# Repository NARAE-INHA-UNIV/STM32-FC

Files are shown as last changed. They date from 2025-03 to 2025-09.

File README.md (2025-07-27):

**본 문서는 STM32 firmware만을 다루고 있습니다.**

> [[STM32-FC-docs]](https://github.com/NARAE-INHA-UNIV/STM32-FC-docs) How to use, Specification <br>
> [[STM32-FC-hw]](https://github.com/NARAE-INHA-UNIV/STM32-FC-hw) KiCAD, Schematic, PCB Artwork <br>
> [[MiniLink_cli]](https://github.com/NARAE-INHA-UNIV/MiniLink_cli) Data analysis like msg, log, param <br>

-----

# STM32 FC

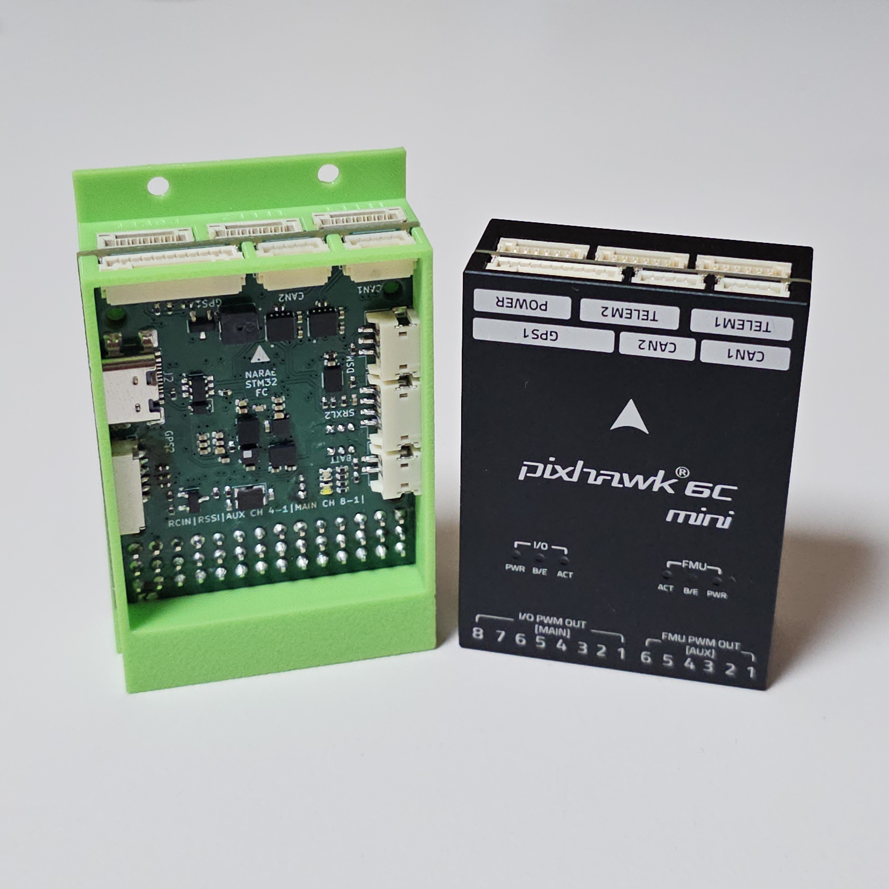
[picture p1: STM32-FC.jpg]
pcb img


인하대학교 모형항공기 동아리 나래에서 2024년 동계 UAV 활동으로 진행한 프로젝트임. <br>
회로와 펌웨어를 개발하되, 기성 pixhawk 모듈과 호환성을 가지기 위해 pixhawk 6C mini의 인터페이스와 흡사하게 제작하는 것을 목표로함. <br>

- 활동명 : [UAV] FC 제작 활동
- 일시 : 2024 동계 방학 - 진행중
- 팀명 :  항공전자 (구 FC)
- 팀장 : 정영우(2025), 이현제(2024)

## 폴더 구조

`Plane` 폴더가 STM32Cube IDE 프로젝트이다. 주로 수정할 코드는 `Core` 디렉토리 내에 위치한다.

`Plane` -> `Core` -> `Src/Inc`

- Src : Source code (.c)
- Inc : header (.h)
  - {Module Name}.h
  - {Module Name}_module.h
  - {Module Name}_common.h
  - {Module Name}_type.h

{Module Name} 앞의 접두사의 의미 :
- `FC` : 보드 내부 HW 관리 (UART, RC, Servo etc.)
- `AP` : 고수준의 제어기나 자율 비행 (Failsafe, RTH etc.)
- `SEN` : 외부 센서

헤더 파일 중 `driver.h`는 외부 모듈에서 접근할 떄 사용한다. <br>
예를 들어 `main.c`가 `RadioContol` 모듈에 접근할 때 `FC_RC/driver.h`에 접근해야 한다. `RadioContol.h`는 해당 모듈 내부에서 사용하는 코드로 외부에서 직접 접근하지 않도록 한다.

```bash
├─AP_Failsafe       # Failsafe 관련 코드
├─FC_AHRS           # IMU 센서, 기압 센서
├─FC_Basic          # Buzzer나 LED 등
├─FC_RC             # 라디오 조종기 (스펙트럼, PPM, ELRS)
├─FC_Servo          # 서보 모터, ESC
├─FC_Serial         # Serial 기능
│  └─MiniLink       # 외부 장치와 통신하는 프로토콜
│      └─Param      # 파라미터 관리
└─test              # 테스트 중인 코드
```

## 기여 (개발)

1. 프로젝트 fork
2. fork된 개인 레파지토리 clone
3. 코드 작성
4. 개인 레파지토리에 커밋 & 푸시
5. Pull-request

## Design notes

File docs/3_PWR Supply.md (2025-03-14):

# 3. 전원 공급시 주의사항

| **보드는 하나의 전원으로부터 5V를 공급 받아야 한다.**

보드는 `5V` 라인과  `5V_PWR` 라인으로 나뉜다.
- `5V` 라인은 칩셋과 센서 등 내부 장치와 GPS, 텔레메트리 등 외부장치를 구동한다.
- `5V_PWR`은 ESC와 서보모터 등 `SERVO OUT` 핀에 연결되어 있다.
- 일반적으로 `5V`와 `5V_PWR`은 분리되어 있으나, 필요에 따라 스위치를 통해 연결할 수 있다. 이 경우 둘 이상의 전원이 발생하지 않도록 유의한다.

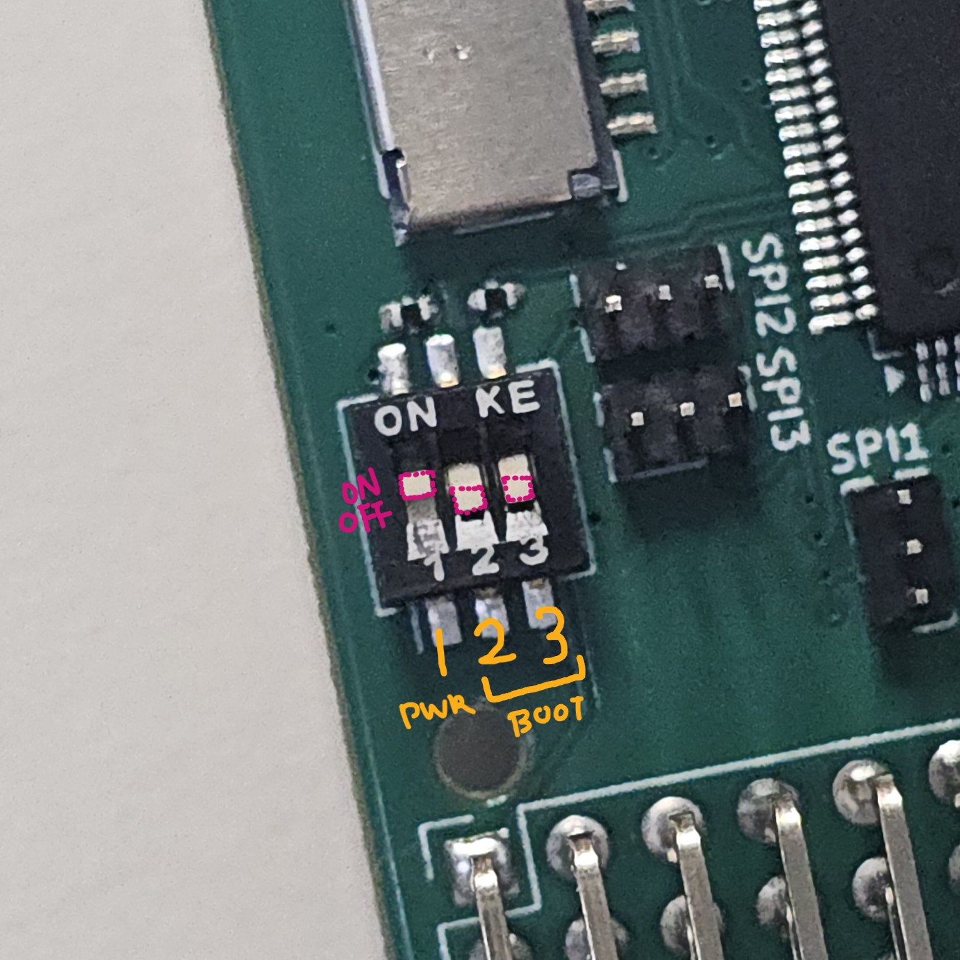
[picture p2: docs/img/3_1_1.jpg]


스위치 1번이 두 전원 라인을 연결하는 데 사용한다. 일반적으로 `OFF` 상태가 기본값이다. 

- ON : 연결
- OFF (Default) : 차단

보드에서 `SERVO OUT` 측 기기로 전원을 공급하거나, `SERVO OUT`에 연결된 ESC로부터 전원을 공급 받을 때 `ON`으로 변경한다.

아래는 전원을 공급하는 세가지 방법에 대해 설명한다.

## 1. USB를 통한 공급 (개발용)

USB를 통해 전원을 공급할 수 있다. 이 경우에 다음 사항에 유의해야 한다.
- USB A to C 케이블만 사용 가능
- 고부하 사용 금지

USB 선을 통해 공급할 수 있는 전력의 한계가 있으므로, 별도의 전원 없이 다수의 서보 모터를 구동하면 보드가 손상될 수 있다.

별도의 배터리가 필요 없어 개발 과정에서 유용하지만, 비행할 수 없으므로 후술할 방법도 익혀야한다.

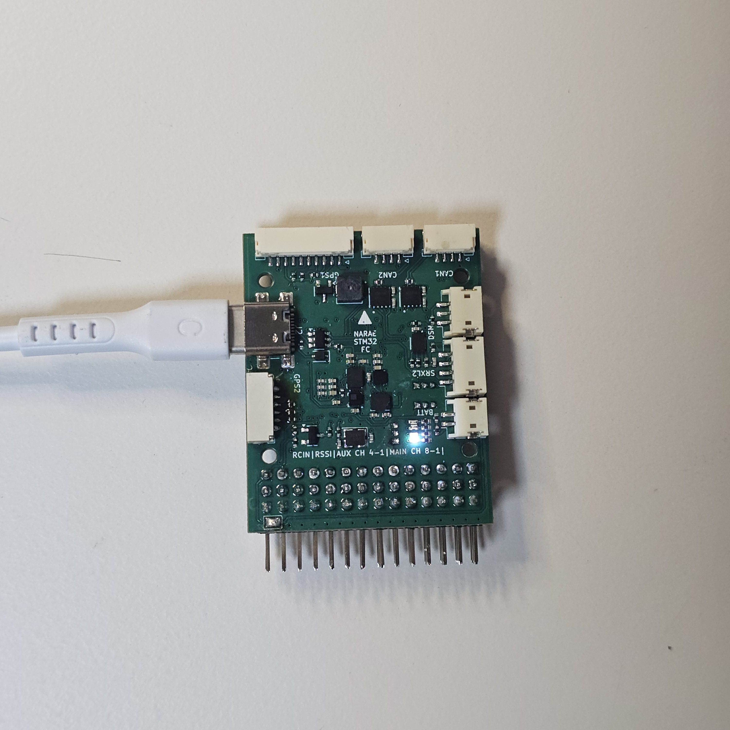
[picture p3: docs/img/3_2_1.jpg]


## 2. 픽스호크의 파워모듈을 통한 공급 (권장)

픽스호크(Pixhawk)사의 파워모듈을 통해 전원을 공급하는 것으로 가장 안전하므로 권장하는 방법이다. 

픽스호크에는 다양한 파워모듈이 존재하며, 이중 **아날로그 모듈**을 사용해야 한다. 예를 들어 `PM02`와 `PM02D`에서 PM02D는 디지털 버전이므로 사용할 수 없다. 두 모델은 연결 커넥터가 다르므로 혼용할 가능성은 없다.

권장하는 모델은 다음과 같다.
- 1개의 ESC와 모터를 사용하는 단발 고정익기인 경우 : PM02
- 2개 이상의 ESC를 사용하는 고정익기 또는 멀티콥터 : PM06

파워 모듈은 보드의 `POWER` 커넥터에 연결한다.

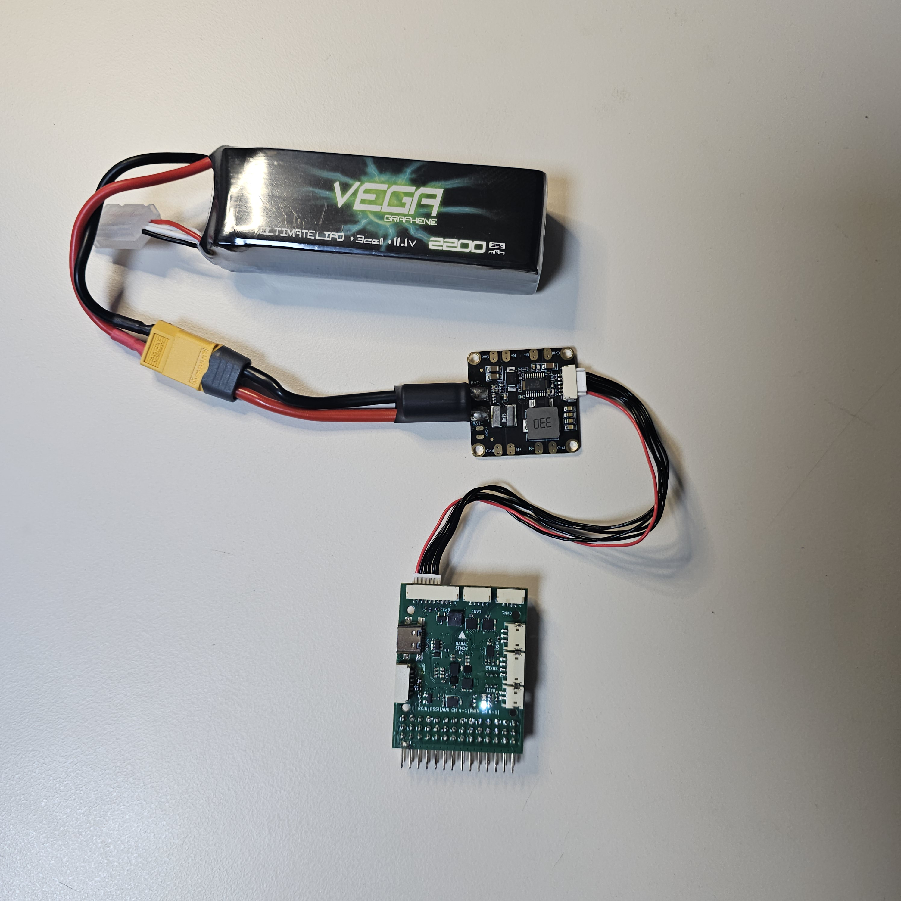
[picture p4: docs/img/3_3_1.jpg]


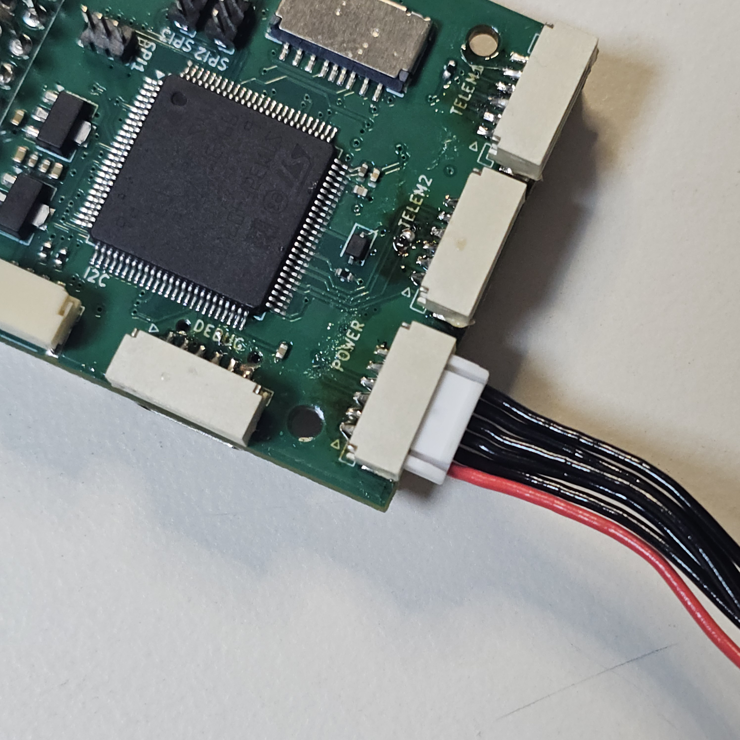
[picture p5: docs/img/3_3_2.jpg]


## 3. ESC를 통한 공급

BEC가 내장된 ESC로부터 전원을 공급받는 방법으로, 가장 간단하나 주의가 요구된다.

- 5V BEC 내장 ESC만 사용
- ESC와 모터는 하나만 사용
- 스위치 1번을 ON 상태로 조정한다.
- PWM 단자 중 왼쪽 두 개는 사용하면 안됨.
- PWM 단자는 -, +, ~ (GND, 5V_PWR, Signal) 순서임.

이 방법은 단발 고정익 이나 회전익 기체에만 사용할 수 있다.
즉, 둘 이상의 ESC와 모터를 사용하는 고정익기 또는 멀티콥터는 반드시 파워 모듈을 사용해야 한다. 

PWM 단자 중 왼쪽 두 개는 `RCIN`과 `RSSI` 이므로 사용하면 안된다. `AUX`과 `MAIN`의 `SERVO OUT`에 연결하여 사용한다.

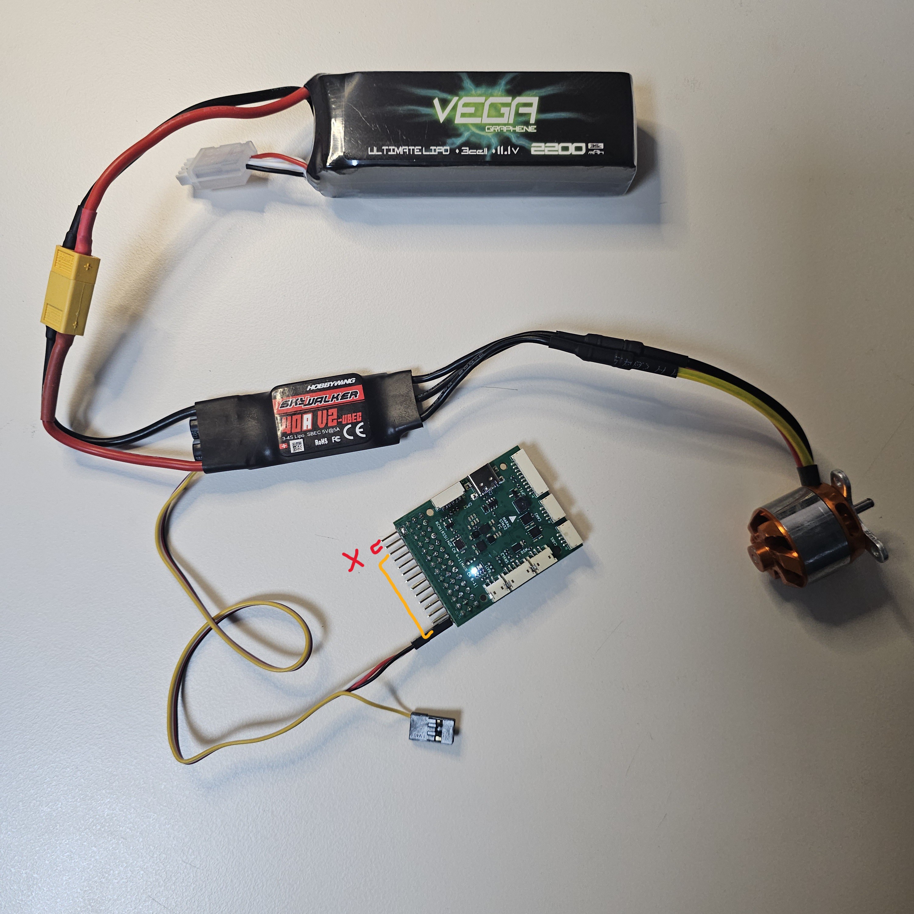
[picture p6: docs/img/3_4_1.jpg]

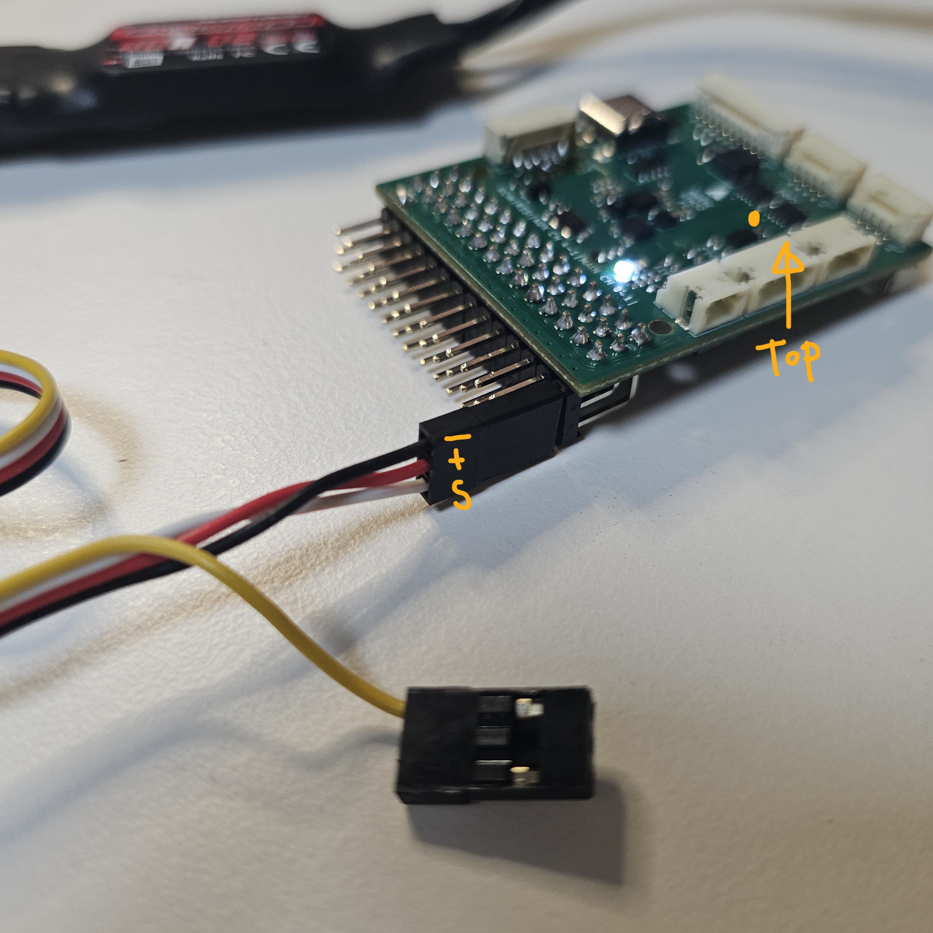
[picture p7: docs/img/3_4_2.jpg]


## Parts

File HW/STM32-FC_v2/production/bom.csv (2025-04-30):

Designator | Footprint | Quantity | Value | LCSC Part #
BZ1 | FUET-4020 | 1 | FUET-4020 | C391027
C1, C4 | 0402 | 2 | 10pF | C1545
C10, C11, C13, C20, C21, C22, C24, C29, C3, C30, C32, C33, C34, C35, C5, C8, C9 | 0402 | 17 | 100nF | C1525
C12 | 0402 | 1 | 1uF | C14445
C14, C15, C16, C27 | 0402 | 4 | 4.7uF | C307423
C17, C18, C19, C2, C28 | 0402 | 5 | 10uF | C307415
C23 | 0402 | 1 | 100pF | C152819
C25 | 0402 | 1 | 2.2nF | C84703
C26 | 0402 | 1 | 10nF | C15195
C31 | 0402 | 1 | 220nF | C16651
C6, C7 | 0402 | 2 | 2.2uF | C170151
D1, D5, D6 | D_SOD-323 | 3 | B5819W | C22624
D2 | 0402 | 1 | Red | C130719
D3 | 0402 | 1 | Yellow | C130721
D4 | 0402 | 1 | Green | C130722
J1, J10, J11, J12, J3 | JST_GH_SM06B-GHS-TB_06x1.25mm_Angled | 5 | GH 1.25mm 6P | C133065
J13, J14, J15, J16 | JST_GH_SM04B-GHS-TB_04x1.25mm_Angled | 4 | GH 1.25mm 4P | C189895
J2 | USB_C_Receptacle_GCT_USB4110 | 1 | USB_C_USB2.0_14P | C709031
J4 | TF06A | 1 | TF-06A | C693844
J5 | JST_ZH_S2B-ZR-SM4A-TF_1x02-1MP_P1.50mm_Horizontal | 1 | JST ZH 1.5mm 2P | C265329
J6 | PWM_Conn_3x14 | 1 | PWM_Conn_3x14 | C3327492
J7 | JST_ZH_S4B-ZR-SM4A-TF_1x04-1MP_P1.50mm_Horizontal | 1 | ZH 1.5mm 4P | C485354
J8 | JST_ZH_S3B-ZR-SM4A-TF_1x03-1MP_P1.50mm_Horizontal | 1 | ZH 1.5mm 3P | C72591
J9 | JST_GH_SM10B-GHS-TB_10x1.25mm_Angled | 1 | GH 1.25mm 10P | C2683602
L1, L2, L3 | VLS201610ET-2R2M | 3 | 2.2u | C114768
Q1, Q2 | Nexperia_SOT1118 | 2 | PMDPB30XN | C478009
Q3 | Nexperia_SOT1118 | 1 | PMDPB55XP | C552752
R1, R11, R12, R2, R23, R24, R25, R26, R27, R28, R31, R32, R34, R36, R37, R38, R39, R40, R41, R42, R43, R44, R45, R46, R47, R5 | 0402 | 26 | 10k | C25531
R10, R3, R33, R4, R48, R49, R6, R7, R8, R9 | 0402 | 10 | 120 | C25079
R13, R14 | 0402 | 2 | 5k1 | C25905
R15, R16, R17, R18, R30, R35 | 0402 | 6 | 1k | C106235
R19 | 0402 | 1 | 1k5 | C25867
R20, R21, R22 | 0402 | 3 | 267k | C2998050
R29 | 0402 | 1 | 15k | C25539
U1 | LQFP-100_14x14mm_P0.5mm | 1 | STM32F407VETx | C28730
U10 | ST_HLGA-10_2x2mm_P0.5mm_LayoutBorder3x2y | 1 | LPS22HH | C2827824
U11 | TMUX1104 | 1 | TMUX1104 | C2865387
U12, U13 | VDFN8_3X3_MCH-L | 2 | ATA6561-GBQW | C617297
U2 | SOT-23-6 | 1 | USBLC6-2SC6 | C7519
U3, U4, U5 | Texas_DSBGA-6_0.855x1.255mm_Layout2x3_P0.4mm_LevelC | 3 | TPS62840 | C2071139
U6 | USON_LUXIG TR_WIN-L | 1 | W25X40CLUXIG | C401661
U7 | BMI323_L | 1 | BMI323 | C5368700
U8 | IIM42352_L | 1 | ICM-42688-P | C1850418
U9 | LIS2MDLTR | 1 | LIS2MDLTR | C919695
Y1 | Crystal_SMD_Abracon_ABM8G-4Pin_3.2x2.5mm | 1 | 16MHz | C1985423

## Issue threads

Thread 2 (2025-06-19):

LPS22HH 동작 안함.

leecurrent04, 2025-06-19:
[[Taiga] LPS22HH 기압계 동작 안함](https://taiga.naraeinha.cc/project/hanggongjeonja/issue/134)

LPS22HH 기압계 Software 리셋 안됨.
---------------------------

SW 리셋이 동작하지 않아, 센서 값도 0으로 출력되는 듯.

[코드](https://github.com/INHA-NARAE/STM32-FC/blob/main/SW/Plane/Core/Src/FC_AHRS/FC_Baro/LPS22HH/LPS22HH.c#L45)

```c
// STM32-FC/SW/Plane/Core/Src/FC_AHRS/FC_Baro/LPS22HH/LPS22HH.c

// Software Reset LPS22HH
temp_reg = LPS22HH_Readbyte(CTRL_REG2);
temp_reg = temp_reg | 0x04;
LPS22HH_Writebyte(CTRL_REG2, temp_reg);
while((LPS22HH_Readbyte(CTRL_REG2)&0x04)!=0x00){
}
```

데이터시트에 따르면,  SW 리셋 비트를 1로 설정하면 리셋 동작이 수행되고 비트가 0으로 되어야 한다.
그러나 비트가 0으로 안 변함.

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

### 로직 분석

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

첫번째 초록색 : 0x91 CTRL\_REG2 값 요청, 0x10 응답
첫번째 파란색 : 0x11 0x14 CTRL\_REG2에 0x14 쓰기 (SW 리셋 명령)
두번째 초록색 : 0x91 CTRL\_REG2 값 요청, 0x14 응답 (SW 리셋 중)
이하 반복

### 예상 원인

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

전원부 커패시터 이상으로 추정.
VDD 및 VDDIO에 각각 100nF 커패시터 연결 권장.
VDD에 4.7uF 커패시터 추가 권장.
그러나 실제 구현된 회로에서는 4.7uF만 연결됨.

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

커패시터 교체 후 동일 증상 시, 전류 부족일 수도 있음.
AHRS 용 별도 3.3V 레귤레이터 도입

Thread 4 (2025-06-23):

BMI323 에러

leecurrent04, 2025-06-23:
# 증상

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

BMI323 센서 값이 -1.0, 1.0으로 출력 됨.

초기 연결 이후, 일정 시간 경과시 문제 발생하는 것으로 추정됨.

# 특이점

로직 아날라이저 연결 후 부팅시, **증상 재현 안됨**.
증상 발현 후 로직 아날라이저 연결 시 MOSI 신호 에러

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

leecurrent04, 2025-07-25:
같은 SPI3 라인에 있는 LIS2MDF 센서의 기본 동작이 3-wire SPI 그랬던 것으로 추정됨.
해당 센서의 동작 모드를 4-wire SPI 설정하니 문제가 발생하지 않음.

Closed 2025-07-25.

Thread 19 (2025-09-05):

bug: roll, pitch에 따른 yaw 변동

sungho2574, 2025-09-05:
yaw는 그대로 둔 상테에서 roll, pitch에만 변화를 줘도 yaw가 같이 변합니다.
yaw축 pid 튜닝을 하기 전에 이 부분이 먼저 해결되어야 할 것 같습니다.

- 아래는 pitch에만 변화를 줄 때의 그래프입니다.
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

- 아래는 roll에만 변화를 줄 때의 그래프입니다.
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

그래프 캡쳐를 좀 잘못했는데 빨간색이 roll, 초록색이 pitch, 파란색이 yaw입니다.

leecurrent04, 2025-09-09:
지금 YAW 계산을 지자계와 roll+pitch로 계산하고 있는데,
지자계 값도 보정이 잘 안되어 있어요.

https://discord.com/channels/1289170468883927081/1289172196484186133/1413210099148914728

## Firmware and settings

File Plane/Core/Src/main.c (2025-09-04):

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
/* Includes ------------------------------------------------------------------*/
#include "main.h"
#include "usb_device.h"

/* USER CODE BEGIN Includes */
#include "usbd_cdc_if.h"

#include <FC_AHRS/AHRS.h>
#include <FC_Basic/Buzzer/Buzzer.h>
#include <FC_Basic/LED/LED.h>
#include <AP_Failsafe/Failsafe.h>
#include <FC_RC/RC.h>
#include <FC_Serial/MiniLink/MiniLink.h>

#include <FC_Serial/Serial.h>
#include <FC_Servo/Servo.h>



/* USER CODE END Includes */

/* USER CODE BEGIN PTD */
int _write(int file, char *p, int len)
{
#define PRINT_CDC 1
#if PRINT_CDC == 0
	for(int i=0; i<len; i++)
	{
		while(!LL_USART_IsActiveFlag_TXE(USART2));
		LL_USART_TransmitData8(USART2, *(p+i));
	}
#else
	static uint8_t* prePacket = 0;
	static uint16_t preLenth = 0;

	uint8_t* temp = prePacket;
	prePacket = (uint8_t*)malloc((len+preLenth)*sizeof(uint8_t));

	memcpy(prePacket, temp, preLenth);
	memcpy(prePacket+preLenth, p, len);

	free(temp);
	preLenth += len;

	if (USBD_OK == CDC_Transmit_FS((uint8_t*)prePacket, preLenth)) {
		preLenth = 0;
		return preLenth;
	}

	return -1;
#endif
}

/* USER CODE END PTD */


CAN_HandleTypeDef hcan1;
CAN_HandleTypeDef hcan2;

void SystemClock_Config(void);
static void MX_GPIO_Init(void);
static void MX_USART1_UART_Init(void);
static void MX_USART2_UART_Init(void);
static void MX_USART3_UART_Init(void);
static void MX_UART4_Init(void);
static void MX_UART5_Init(void);
static void MX_SPI1_Init(void);
static void MX_SPI2_Init(void);
static void MX_SPI3_Init(void);
static void MX_TIM1_Init(void);
static void MX_TIM3_Init(void);
static void MX_TIM4_Init(void);
static void MX_TIM5_Init(void);
static void MX_TIM13_Init(void);
static void MX_TIM14_Init(void);
static void MX_I2C1_Init(void);
static void MX_I2C2_Init(void);
static void MX_I2C3_Init(void);
static void MX_ADC1_Init(void);
static void MX_CAN1_Init(void);
static void MX_CAN2_Init(void);
/* USER CODE BEGIN PFP */
extern int PARM_load(void);
/* USER CODE END PFP */

/**
  * @brief  The application entry point.
  * @retval int
  */
int main(void)
{

  /* MCU Configuration--------------------------------------------------------*/

  /* Reset of all peripherals, Initializes the Flash interface and the Systick. */
  HAL_Init();

  /* Configure the system clock */
  SystemClock_Config();

  /* Initialize all configured peripherals */
  MX_GPIO_Init();
  MX_USART1_UART_Init();
  MX_USART2_UART_Init();
  MX_USART3_UART_Init();
  MX_UART4_Init();
  MX_UART5_Init();
  MX_SPI1_Init();
  MX_SPI2_Init();
  MX_SPI3_Init();
  MX_TIM1_Init();
  MX_TIM3_Init();
  MX_TIM4_Init();
  MX_TIM5_Init();
  MX_TIM13_Init();
  MX_TIM14_Init();
  MX_I2C1_Init();
  MX_I2C2_Init();
  MX_I2C3_Init();
  MX_ADC1_Init();
  MX_CAN1_Init();
  MX_CAN2_Init();
  MX_USB_DEVICE_Init();
  /* USER CODE BEGIN 2 */

  LL_TIM_EnableCounter(TIM4);
  LL_TIM_EnableCounter(TIM13);
  LL_TIM_EnableCounter(TIM14);

  PARM_load();

  BuzzerPlayInit();

  /* INITIAILIZE  BEGIN */
  SERIAL_Initialization();

  SERVO_Initialization();

  RC_Initialization();
  AHRS_Initialization();

  /* INITIAILIZE  END */
  BuzzerPlayOneCycle();
  SERVO_doArm();

  LED_SetYellow(1);

  /* USER CODE END 2 */

  /* Infinite loop */
  /* USER CODE BEGIN WHILE */
  while (1)
  {
	  RC_GetData();
	  AHRS_GetData();

	  if(FS_IsFailsafe() == 0){
		  SERVO_control();
	  }

	  SERIAL_Handler();
	  LED_Update();

    /* USER CODE END WHILE */

    /* USER CODE BEGIN 3 */
  }
  /* USER CODE END 3 */
}

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


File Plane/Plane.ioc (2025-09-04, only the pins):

Mcu.UserName=STM32F407VETx
PA0-WKUP.GPIO_Label=MAIN_CH5
PA0-WKUP.Signal=S_TIM5_CH1
PA1.GPIO_Label=MAIN_CH6
PA1.Signal=S_TIM5_CH2
PA11.Signal=USB_OTG_FS_DM
PA12.Signal=USB_OTG_FS_DP
PA13.Signal=SYS_JTMS-SWDIO
PA14.Signal=SYS_JTCK-SWCLK
PA2.GPIO_Label=MAIN_CH7
PA2.Signal=S_TIM5_CH3
PA3.GPIO_Label=MAIN_CH8
PA3.Signal=S_TIM5_CH4
PA5.Signal=SPI1_SCK
PA6.Signal=SPI1_MISO
PA7.Signal=SPI1_MOSI
PA8.GPIO_Label=GPS1_SCL
PA8.Signal=I2C3_SCL
PA9.GPIO_Label=RC_SRXL2
PA9.Signal=USART1_TX
PB0.GPIO_Label=MAIN_CH9
PB0.Signal=S_TIM3_CH3
PB1.GPIO_Label=MAIN_CH10
PB1.Signal=S_TIM3_CH4
PB10.GPIO_Label=GPS2_SCL
PB10.Signal=I2C2_SCL
PB11.GPIO_Label=GPS2_SCL
PB11.Signal=I2C2_SDA
PB12.Signal=CAN2_RX
PB13.Signal=SPI2_SCK
PB14.Signal=SPI2_MISO
PB15.Signal=SPI2_MOSI
PB3.Signal=SPI3_SCK
PB4.Signal=SPI3_MISO
PB5.Signal=SPI3_MOSI
PB6.Signal=CAN2_TX
PB7.GPIO_Label=MAIN_CH1
PB7.Signal=S_TIM4_CH2
PB8.Signal=I2C1_SCL
PB9.Signal=I2C1_SDA
PC0.GPIO_Label=V_BATT
PC0.Signal=ADCx_IN10
PC1.GPIO_Label=RSSI
PC1.Signal=ADCx_IN11
PC10.GPIO_Label=GPS1_TX
PC10.Signal=UART4_TX
PC11.GPIO_Label=GPS1_RX
PC11.Signal=UART4_RX
PC12.GPIO_Label=GPS2_TX
PC12.Signal=UART5_TX
PC13-ANTI_TAMP.GPIO_Label=FLASH_NSS
PC13-ANTI_TAMP.Signal=GPIO_Output
PC15-OSC32_OUT.GPIO_Label=MSD_DETECT
PC15-OSC32_OUT.Signal=GPIO_Input
PC2.GPIO_Label=PM_CURRENT
PC2.Signal=ADCx_IN12
PC3.GPIO_Label=PM_VOLTAGE
PC3.Signal=ADCx_IN13
PC4.GPIO_Label=CAN1_STBY
PC4.Signal=GPIO_Output
PC5.GPIO_Label=CAN2_STBY
PC5.Signal=GPIO_Output
PC6.GPIO_Label=MAIN_CH2
PC6.Signal=S_TIM3_CH1
PC7.GPIO_Label=MAIN_CH3
PC7.Signal=S_TIM3_CH2
PC9.GPIO_Label=GPS1_SDA
PC9.Signal=I2C3_SDA
PD0.Signal=CAN1_RX
PD1.Signal=CAN1_TX
PD10.GPIO_Label=GPS1_SW_LED 
PD10.Signal=GPIO_Output
PD11.Signal=USART3_CTS
PD12.Signal=USART3_RTS
PD13.GPIO_Label=GPS1_SW
PD13.Signal=GPIO_Input
PD14.GPIO_Label=Buzzer
PD14.Signal=S_TIM4_CH3
PD15.GPIO_Label=MAIN_CH4
PD15.Signal=S_TIM4_CH4
PD2.GPIO_Label=GPS2_RX
PD2.Signal=UART5_RX
PD3.Signal=USART2_CTS
PD4.Signal=USART2_RTS
PD5.GPIO_Label=Telm1_TX
PD5.Signal=USART2_TX
PD6.GPIO_Label=Telm1_RX
PD6.Signal=USART2_RX
PD8.GPIO_Label=Telm2_TX
PD8.Signal=USART3_TX
PD9.GPIO_Label=Telm2_RX
PD9.Signal=USART3_RX
PE0.GPIO_Label=LED_RED
PE0.Signal=GPIO_Output
PE1.GPIO_Label=LED_YELLOW
PE1.Signal=GPIO_Output
PE11.GPIO_Label=MAIN_CH11
PE11.Signal=S_TIM1_CH2
PE13.GPIO_Label=MAIN_CH12
PE13.Signal=S_TIM1_CH3
PE14.GPIO_Label=PPM_IN
PE14.Signal=GPXTI14
PE2.GPIO_Label=LED_BLUE
PE2.Signal=GPIO_Output
PE3.GPIO_Label=GYRO2_NSS
PE3.Signal=GPIO_Output
PE4.GPIO_Label=MAG_NSS
PE4.Signal=GPIO_Output
PE5.GPIO_Label=GYRO1_NSS
PE5.Signal=GPIO_Output
PE6.GPIO_Label=BARO_NSS
PE6.Signal=GPIO_Output
PE7.GPIO_Label=BARO_INT
PE7.Signal=GPIO_Input
PH0-OSC_IN.Signal=RCC_OSC_IN
PH1-OSC_OUT.Signal=RCC_OSC_OUT

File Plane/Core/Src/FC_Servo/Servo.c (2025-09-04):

/*
 * Servo.c
 *
 *  Created on: Mar 27, 2025
 *      Author: leecurrent04
 *      Email : leecurrent04@inha.edu
 */


/* Includes ------------------------------------------------------------------*/
#include <FC_Servo/Servo_module.h>


/* Variables -----------------------------------------------------------------*/
/*
 * 0x[타이머][채널]
 * 타미머 : 1,3-5
 * 채널 : 1-4
 */
const uint8_t SERVO_TIMER_MAP[SERVO_CHANNEL_MAX] = {
		0x42, 0x31, 0x32, 0x44,
		0x51, 0x52, 0x53, 0x54,
		0x33, 0x34, 0x12, 0x14
};


/* Functions -----------------------------------------------------------------*/
/*
 * @brief SERVO 초기화
 * @detail 출력 프로토콜, 주기 변경
 * @parm none
 * @retval none
 */
int SERVO_Initialization(void)
{
	// PARAM_SERVO* servo = &paramServo;

	LL_TIM_EnableCounter(TIM1);
	LL_TIM_EnableCounter(TIM3);
	LL_TIM_EnableCounter(TIM5);

	if(!(LL_TIM_IsEnabledCounter(TIM1) &&
			LL_TIM_IsEnabledCounter(TIM3) &&
			LL_TIM_IsEnabledCounter(TIM4) &&
			LL_TIM_IsEnabledCounter(TIM5)
			)) return -1;

	SERVO_doDisarm();

	return 0;
}


/*
 * @brief 모든 채널 출력 활성화
 * @parm none
 * @retval none
 */
void SERVO_doArm(void)
{
	configurePWM(param.servo.RATE);

	for(uint8_t i=0; i<SERVO_CHANNEL_MAX; i++)
	{
	    // 해당 서보 채널이 활성화되어 있지 않으면 다음으로 건너뜀.
		if(!((param.servo.GPIO_MASK >> i)&0x1)){
			continue;
		}

		doArm2Channel(i+1, 1);
	}
	return;
}


/*
 * @brief 모든 출력 비활성화
 * @detail 출력 프로토콜 따라 수행
 * @parm none
 * @retval none
 */
void SERVO_doDisarm(void)
{
	configurePWM(param.servo.RATE);

	for(uint8_t i=0; i<SERVO_CHANNEL_MAX; i++)
	{
		doArm2Channel(i+1, 0);
	}
	return;
}

/*
 * @brief SERVO 출력
 * @detail 출력 프로토콜 따라 수행
 * @parm none
 * @retval none
 */
void SERVO_control(void)
{
	calculateServoOutput();

	setPWM();
	return;
}


/*
 * @brief Fail-Safe 동작
 * @retval none
 */
void SERVO_setFailsafe(void)
{
	setPWM2Channel(1, 1000);
	setPWM2Channel(2, 1500);
	setPWM2Channel(3, 1500);
	setPWM2Channel(4, 1500);
	return;
}


/*
 * @brief ESC Calibration
 * @parm uint8_t mode
 * 				0 : high 신호 입력
 * 				1 : low 신호 입력
 * @retval none
 */
void SERVO_doCalibrate(uint8_t mode)
{
	uint8_t channels[] = {1,2,3,4};
	if(mode)
	{
		configurePWM(50);

		doArm2Channels(&channels[0], sizeof(channels), 1);
		setPWM2Channels(&channels[0], sizeof(channels), 2000);
	}
	else
	{
		setPWM2Channels(&channels[0], sizeof(channels), 1000);
		HAL_Delay(1000);
		doArm2Channels(&channels[0], sizeof(channels), 0);
	}
	return;
}

/* Functions -----------------------------------------------------------------*/
/*
 * @brief 특정 채널 출력 모드 설정
 * @parm uint8_t servoCh (in 1-12)
 * @parm uint8_t state
 * 					0 : enable
 * 					1 : disable
 * @retval 0 : 설정됨
 * @retval -1 : ch 범위 오류
 */
int doArm2Channel(uint8_t servoCh, uint8_t state)
{
	if(servoCh<1 || servoCh>12) return -1;
	const TIM_TypeDef* timerArr[] = {
			0, TIM1, 0, TIM3, TIM4, TIM5
	};

	// map에서 상위 비트로 타이머 선택
	TIM_TypeDef* timer = (TIM_TypeDef*)timerArr[SERVO_TIMER_MAP[servoCh-1]>>4];

	// map에서 하위 비트로 채널 선택
	uint32_t ch;
	switch(SERVO_TIMER_MAP[servoCh-1]&0x0F){
	case 1: ch = LL_TIM_CHANNEL_CH1; break;
	case 2: ch = LL_TIM_CHANNEL_CH2; break;
	case 3: ch = LL_TIM_CHANNEL_CH3; break;
	case 4: ch = LL_TIM_CHANNEL_CH4; break;
	default: ch = 0; break;
	}

	if(timer&&ch){
		if(state == 1) LL_TIM_CC_EnableChannel(timer, ch);
		else if(state == 0) LL_TIM_CC_DisableChannel(timer, ch);
	}

	LL_TIM_GenerateEvent_UPDATE(TIM1);
	LL_TIM_GenerateEvent_UPDATE(TIM3);
	LL_TIM_GenerateEvent_UPDATE(TIM4);
	LL_TIM_GenerateEvent_UPDATE(TIM5);

	return 0;
}


/*
 * @brief 특정 채널 출력 모드 설정
 * @parm uint8_t* pCh (each in 1-12)
 * @parm uint8_t len : array size
 * @parm uint8_t state
 * 					0 : enable
 * 					1 : disable
 * @retval 0 : 설정됨
 */
int doArm2Channels(uint8_t *pCh, uint8_t len, uint8_t state)
{
	for(uint8_t i=0; i<len; i++)
	{
		uint8_t ch = pCh[i];
		doArm2Channel(ch, state);
	}
	return 0;
}


/*
 * @brief PWM 주기 설정
 * @detail 50-490Hz까지 변경
 * @parm uint16_t hz (in 50-490)
 * @retval 0 : 설정됨
 * @retval 1 : 주파수 범위 오설정
 */
uint8_t configurePWM(uint16_t hz)
{
	if(hz>490 || hz<50) return 1;

	// (추가) PPM 입력이 활성화 되어 있으면 50Hz 고정하도록
	LL_TIM_SetAutoReload(TIM1, 1000000/hz-1);
	LL_TIM_SetAutoReload(TIM3, 1000000/hz-1);
	LL_TIM_SetAutoReload(TIM4, 1000000/hz-1);
	LL_TIM_SetAutoReload(TIM5, 1000000/hz-1);

	LL_TIM_SetPrescaler(TIM1, 168-1);
	LL_TIM_SetPrescaler(TIM3, 84-1);
	LL_TIM_SetPrescaler(TIM4, 84-1);
	LL_TIM_SetPrescaler(TIM5, 84-1);

	LL_TIM_GenerateEvent_UPDATE(TIM1);
	LL_TIM_GenerateEvent_UPDATE(TIM3);
	LL_TIM_GenerateEvent_UPDATE(TIM4);
	LL_TIM_GenerateEvent_UPDATE(TIM5);

	return 0;
}


/*
 * @brief 출력할 값(CCR) 계산
 * @detail
 * @parm none
 * @retval none
 */
void calculateServoOutput(void)
{
	msg.servo_output_raw.time_usec = msg.system_time.time_boot_ms;

	for(uint8_t i=0; i<SERVO_CHANNEL_MAX; i++)
	{
		// 해당 서보 채널이 활성화되어 있지 않으면 다음으로 건너뜀.
		if(!((param.servo.GPIO_MASK >> i)&0x1)){
			continue;
		}

		msg.servo_output_raw.servo_raw[i] = Servo_nomalize(msg.RC_channels.value[i]);
		// servo_output_raw.servo_raw[i] = scaled_imu + RC_channels 를 기반으로 요리조리 계산해서 결정.
	}

	// Quad-Copter motor mixer
	uint16_t thr;
	uint16_t pit;
	uint16_t rol;
	uint16_t yaw;
	if(param.rc.PROTOCOLS != 0)
	{
		thr = Servo_nomalize(msg.RC_channels.value[param.rc.map.THR]);
		pit = Servo_nomalize(msg.RC_channels.value[param.rc.map.PIT]);
		rol = Servo_nomalize(msg.RC_channels.value[param.rc.map.ROL]);
		yaw = Servo_nomalize(msg.RC_channels.value[param.rc.map.YAW]);
	}
	else
	{
		thr = 1500;
		pit = 1500;
		rol = 1500;
		yaw = 1500;
	}
	const int16_t ang_r = msg.attitude.roll * 10;
	const int16_t ang_p = msg.attitude.pitch * 10;
	const int16_t ang_y = msg.attitude.yaw * 10;

	msg.servo_output_raw.servo_raw[0] = 1000 + (thr-1000)*1.0 - (pit-1500)*0.6 - (rol-1500)*0.6 + (yaw-1500)*0.6 + ang_r - ang_p;
	msg.servo_output_raw.servo_raw[1] = 1000 + (thr-1000)*1.0 + (pit-1500)*0.6 + (rol-1500)*0.6 + (yaw-1500)*0.6 - ang_r + ang_p;
	msg.servo_output_raw.servo_raw[2] = 1000 + (thr-1000)*1.0 - (pit-1500)*0.6 + (rol-1500)*0.6 - (yaw-1500)*0.6 - ang_r - ang_p;
	msg.servo_output_raw.servo_raw[3] = 1000 + (thr-1000)*1.0 + (pit-1500)*0.6 - (rol-1500)*0.6 - (yaw-1500)*0.6 + ang_r + ang_p;

	msg.servo_output_raw.servo_raw[0] = Servo_nomalize(msg.servo_output_raw.servo_raw[0]);
	msg.servo_output_raw.servo_raw[1] = Servo_nomalize(msg.servo_output_raw.servo_raw[1]);
	msg.servo_output_raw.servo_raw[2] = Servo_nomalize(msg.servo_output_raw.servo_raw[2]);
	msg.servo_output_raw.servo_raw[3] = Servo_nomalize(msg.servo_output_raw.servo_raw[3]);

	return;
}


/*
 * @brief standard PWM 출력
 * @detail
 * @parm none
 * @retval none
 */
void setPWM(void)
{
	for(uint8_t i=0; i<SERVO_CHANNEL_MAX; i++)
	{
		// 해당 서보 채널이 활성화되어 있지 않으면 다음으로 건너뜀.
		if(!((param.servo.GPIO_MASK >> i)&0x1)){
			continue;
		}
		setPWM2Channel(i+1, msg.servo_output_raw.servo_raw[i]);
	}
	return;
}
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

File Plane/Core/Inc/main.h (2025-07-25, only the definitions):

#define LED_BLUE_Pin LL_GPIO_PIN_2
#define LED_BLUE_GPIO_Port GPIOE
#define GYRO2_NSS_Pin LL_GPIO_PIN_3
#define GYRO2_NSS_GPIO_Port GPIOE
#define MAG_NSS_Pin LL_GPIO_PIN_4
#define MAG_NSS_GPIO_Port GPIOE
#define GYRO1_NSS_Pin LL_GPIO_PIN_5
#define GYRO1_NSS_GPIO_Port GPIOE
#define BARO_NSS_Pin LL_GPIO_PIN_6
#define BARO_NSS_GPIO_Port GPIOE
#define FLASH_NSS_Pin LL_GPIO_PIN_13
#define FLASH_NSS_GPIO_Port GPIOC
#define MSD_DETECT_Pin LL_GPIO_PIN_15
#define MSD_DETECT_GPIO_Port GPIOC
#define V_BATT_Pin LL_GPIO_PIN_0
#define V_BATT_GPIO_Port GPIOC
#define RSSI_Pin LL_GPIO_PIN_1
#define RSSI_GPIO_Port GPIOC
#define PM_CURRENT_Pin LL_GPIO_PIN_2
#define PM_CURRENT_GPIO_Port GPIOC
#define PM_VOLTAGE_Pin LL_GPIO_PIN_3
#define PM_VOLTAGE_GPIO_Port GPIOC
#define MAIN_CH5_Pin LL_GPIO_PIN_0
#define MAIN_CH5_GPIO_Port GPIOA
#define MAIN_CH6_Pin LL_GPIO_PIN_1
#define MAIN_CH6_GPIO_Port GPIOA
#define MAIN_CH7_Pin LL_GPIO_PIN_2
#define MAIN_CH7_GPIO_Port GPIOA
#define MAIN_CH8_Pin LL_GPIO_PIN_3
#define MAIN_CH8_GPIO_Port GPIOA
#define CAN1_STBY_Pin LL_GPIO_PIN_4
#define CAN1_STBY_GPIO_Port GPIOC
#define CAN2_STBY_Pin LL_GPIO_PIN_5
#define CAN2_STBY_GPIO_Port GPIOC
#define MAIN_CH9_Pin LL_GPIO_PIN_0
#define MAIN_CH9_GPIO_Port GPIOB
#define MAIN_CH10_Pin LL_GPIO_PIN_1
#define MAIN_CH10_GPIO_Port GPIOB
#define BARO_INT_Pin LL_GPIO_PIN_7
#define BARO_INT_GPIO_Port GPIOE
#define MAIN_CH11_Pin LL_GPIO_PIN_11
#define MAIN_CH11_GPIO_Port GPIOE
#define MAIN_CH12_Pin LL_GPIO_PIN_13
#define MAIN_CH12_GPIO_Port GPIOE
#define PPM_IN_Pin LL_GPIO_PIN_14
#define PPM_IN_GPIO_Port GPIOE
#define PPM_IN_EXTI_IRQn EXTI15_10_IRQn
#define GPS2_SCL_Pin LL_GPIO_PIN_10
#define GPS2_SCL_GPIO_Port GPIOB
#define GPS2_SCLB11_Pin LL_GPIO_PIN_11
#define GPS2_SCLB11_GPIO_Port GPIOB
#define Telm2_TX_Pin LL_GPIO_PIN_8
#define Telm2_TX_GPIO_Port GPIOD
#define Telm2_RX_Pin LL_GPIO_PIN_9
#define Telm2_RX_GPIO_Port GPIOD
#define GPS1_SW_LED_Pin LL_GPIO_PIN_10
#define GPS1_SW_LED_GPIO_Port GPIOD
#define GPS1_SW_Pin LL_GPIO_PIN_13
#define GPS1_SW_GPIO_Port GPIOD
#define Buzzer_Pin LL_GPIO_PIN_14
#define Buzzer_GPIO_Port GPIOD
#define MAIN_CH4_Pin LL_GPIO_PIN_15
#define MAIN_CH4_GPIO_Port GPIOD
#define MAIN_CH2_Pin LL_GPIO_PIN_6
#define MAIN_CH2_GPIO_Port GPIOC
#define MAIN_CH3_Pin LL_GPIO_PIN_7
#define MAIN_CH3_GPIO_Port GPIOC
#define GPS1_SDA_Pin LL_GPIO_PIN_9
#define GPS1_SDA_GPIO_Port GPIOC
#define GPS1_SCL_Pin LL_GPIO_PIN_8
#define GPS1_SCL_GPIO_Port GPIOA
#define RC_SRXL2_Pin LL_GPIO_PIN_9
#define RC_SRXL2_GPIO_Port GPIOA
#define GPS1_TX_Pin LL_GPIO_PIN_10
#define GPS1_TX_GPIO_Port GPIOC
#define GPS1_RX_Pin LL_GPIO_PIN_11
#define GPS1_RX_GPIO_Port GPIOC
#define GPS2_TX_Pin LL_GPIO_PIN_12
#define GPS2_TX_GPIO_Port GPIOC
#define GPS2_RX_Pin LL_GPIO_PIN_2
#define GPS2_RX_GPIO_Port GPIOD
#define Telm1_TX_Pin LL_GPIO_PIN_5
#define Telm1_TX_GPIO_Port GPIOD
#define Telm1_RX_Pin LL_GPIO_PIN_6
#define Telm1_RX_GPIO_Port GPIOD
#define MAIN_CH1_Pin LL_GPIO_PIN_7
#define MAIN_CH1_GPIO_Port GPIOB
#define LED_RED_Pin LL_GPIO_PIN_0
#define LED_RED_GPIO_Port GPIOE
#define LED_YELLOW_Pin LL_GPIO_PIN_1
#define LED_YELLOW_GPIO_Port GPIOE

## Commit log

2025-01-03 RC IN modified
    [STM32-FC.kicad_sch, io_GPS.kicad_sch, io_RC_INPUT.kicad_sch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]
2025-01-03 Big Update:IMU/RC/Conn./MCU
    [1050170001.stp, BMI088.step, LIS2MDLTR.step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]
2025-01-03 2025.01.03v2:PM(Power Module) added
    [STM32-FC.kicad_sch, io_GPS.kicad_sch, io_RC_INPUT.kicad_sch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]
2025-01-06 Baro/SD Card update
    [1050170001.stp, 3x1 Male Pin Header Angle.STEP, 3x1 Male Pin Header.STEP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]
2025-01-16 2025.01.16 JST conn lib added
    [B10B-ZR-SM4-TF.step, B10B-ZR.step, B11B-ZR-SM4-TF.step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]
2025-01-17 2025.01.17 : PCB layout
    [3x14 Male Pin Header Angle.step, STM32-FC.csv, STM32-FC.dsn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]
2025-01-17 2025.01.17 Differential Pair update
    [STM32-FC.dsn, STM32-FC.kicad_pcb, STM32-FC.kicad_sch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]
2025-02-01 2025.02.01 PCB Routing start
    [STM32-FC.dsn, STM32-FC.kicad_pcb, STM32-FC.kicad_sch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]
2025-02-01 2025.02.01 PCB routing update 1
    [STM32-FC.kicad_pcb, STM32-FC.kicad_sch, memory.kicad_sch]
2025-02-03 2025.02.03 PCB routing update 2
    [STM32-FC.kicad_pcb, STM32-FC.kicad_sch]
2025-02-05 2025.02.05 PCB routing 3
    [STM32-FC.kicad_pcb, sensors.kicad_sch]
2025-02-05 2025.02.05 PCB routing done
    [STM32-FC-B_Cu.gbr, STM32-FC-B_Mask.gbr, STM32-FC-B_Paste.gbr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]
2025-02-06 2025.02.06 PCB routing done v2
    [STM32-FC-B_Cu.gbr, STM32-FC-B_Mask.gbr, STM32-FC-B_Paste.gbr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]
2025-02-06 2025.02.06 PCB routing done v3
    [STM32-FC-B_Cu.gbr, STM32-FC-B_Mask.gbr, STM32-FC-B_Paste.gbr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]
2025-02-07 2025.02.07 USB C Conn change v1
    [STM32-FC-B_Cu.gbr, STM32-FC-B_Mask.gbr, STM32-FC-B_Paste.gbr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]
2025-02-07 2025.02.07 USB C Conn chage v2
    [STM32-FC.kicad_pcb, bom.csv, positions.csv]
2025-02-11 2025.02.11 PCB DONE! MEMO UPDATING
    [Pinmap.xlsx, STM32-FC.kicad_pcb, STM32-FC.kicad_sch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]
2025-02-25 Test software v1
    [3x1 Male Pin Header Angle.STEP, 3x1 Male Pin Header.STEP, 3x10 Male Pin Header Angle.STEP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]
2025-03-05 2025.03.05 SW:GYRO TESTING
    [Pinmap.xlsx]
2025-03-09 2025.03.09 : SW SRXL2 failed.
    [Buzzer.c, ICM42688.c, main.c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]
2025-03-14 SRXL2_readByte() array index out bug fix
    [STM32-FC.kicad_pcb, STM32-FC.kicad_sch, sensors.kicad_sch]
2025-03-25 Log add. backup
    [STM32-FC.kicad_pcb, STM32-FC.kicad_sch, io_RC_INPUT.kicad_sch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]
2025-03-27 Servo add
    [Pinmap.xlsx]
2025-03-28 SRXL2 IRQ2 Update & Bug fix
    [RadioControl.c]
2025-03-29 SRXL2 Throttle check & Param udpate
2025-03-29 ESC Calibration with RC add
2025-03-30 Gyro 1 update
2025-04-05 RC Cali&Throttle check improved
2025-04-30 imu ICM42688P dps update
    [3x1 Male Pin Header Angle.STEP, 3x1 Male Pin Header.STEP, 3x10 Male Pin Header Angle.STEP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]
2025-04-30 imu ICM42688P dps update v2
2025-06-04 bug fix about servo output
    [DevTool-B_Cu.gbr, DevTool-B_Mask.gbr, DevTool-B_Paste.gbr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]
2025-06-11 LPS22HH Baro update(WIP) and Radio update
    [sensors.kicad_sch]
2025-06-20 LPS22HH Circuit update
    [NMOS.kicad_sch, NMOS_powerSelector.kicad_sch, PMOS.kicad_sch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]
2025-06-20 HW Lib and RC code refactoring, GCS_log united and BMI323 IMU init.
    [NMOS.kicad_sch, NMOS_powerSelector.kicad_sch, PMOS.kicad_sch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]
2025-07-02 BMI323 Work in progress
    [STM32-FC.kicad_pcb, STM32-FC.kicad_sch, io_GPS.kicad_sch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]
2025-07-02 repo split
    [DevTool-B_Cu.gbr, DevTool-B_Mask.gbr, DevTool-B_Paste.gbr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]
2025-07-22 MAVLink -> MiniLink and fix while bugs in printf with CDC
    [Buzzer.c]
2025-07-23 add : minilink struct
    minilink용 구조체 정의
2025-07-23 add : uart 4&5 interrrupt
    **빌드 성공/테스트 미시행**
    코드 수정이 필요함.
    - UART 4&5(GPS1&2) UART interrupt 추가
    - LPS22, Log.h <main.h> 수정
    - IMU dt 전역 변수 -> 로컬 및 파라미터 인자 전달하도록 수정
2025-07-23 refactor : prepare calibration scaled_imu
    Madwick 코드 리펙토링 중, SCALED_IMU offset 보정 코드가 먼저 필요할 것 같아 백업용 커밋
2025-07-23 refactor : integrate log &param to MiniLink
    - MiniLink : Log, PARAM 코드 통합됨.
    - Airspeed 구조체 선언
    - 무분별한 헤더 파일 참조 수정
    [Buzzer.c]
2025-07-23 test directory
    merge전 테스트가 필요한 코드 작성하는 폴더 생성
2025-07-25 refactor : BMI323
    - BMI323 함수 이름 및 불필요한 코드 리펙토링
    - SPI 코드 리펙토링
2025-07-25 add : led blink!
    - 장치 상태에 따라 LED 점등이 변화하는 코드 작성
    - 상태를 2진수로 본 다음, 각 비트에 해당하는 장치가 오류가 있음을 표현함.
    - 상태가 1이면 0x0001 이므로 1번 장치 이상 : 10-
    - 상태가 2이면 0x0010 이므로 2번 장치 이상 : 1010-
    - 상태가 3이면 0x0011 이므로 1&2번 장치 이상: 10-1010-
    - 상태가 4이면 0x0100 이므로 3번 장치 이상 : 101010-
    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
2025-07-25 bug : multiple led not work
    여러 LED를 키면 동작안함.
    아무래도 이전 시간을 기록하는 변수를 전역으로 사용해서 그런듯.
    [LED.c, Serial.c, main.c]
2025-07-25 fix : bug not working multiple leds
    - LED 여러 개 일때 동작 안 하는 버그 수정.
    - previous_t를 공용 변수로 사용해서 그랬음. 각자 LED 마다 사용해서 해결함.
    - Reset 함수 구현해야함.
    - 함수 이름이 맘에 안듦
    - SetRC -> SetRed 고려
    [LED.c, main.c]
2025-07-26 add : LED_reset()
    - LED_set(0) 명령으로도 가능함.
    - Serial Payload 수신 관련 문제 발견
2025-07-27 Added Filter header file, c file, and filter design diagram to IMU file
2025-07-27 refactor : LKF
    - 최신 커밋 버전으로 업데이트
    - FC_Basic/Matrix 분리
    - LKF_Update(SCALED_IMU* imu) 파라미터 추가
    - LPF 함수 리펙토링
    - LPF_Update(), LPF_init()
2025-07-27 refactor : LPF and translate Eular & Quaternion in AHRS
    - AHRS에서 LPF, 오일러각 및 쿼터니언 변환 호출
    - 혼란을 피하기 위해 오일러2쿼터니언, 쿼터니언2오일러 코드를 비슷하게 수정
    [AHRS.c]
2025-07-27 rename : all header file name
    - driver.h -> 모듈.h
    - 모듈.h -> 모듈_module.h
    예를 들어 AHRS.h -> AHRS_module.h
    AHRS/driver.h -> AHRS.h
2025-07-27 fix : eular not working
    First tested
    [AHRS.c, BMI323.c, ICM42688P.c]
2025-08-02 refactor & begin calibrate ICM-42688-P
    - minor refactor in IMU
    - begin to add calibartion funciton for ICM-42688-P
2025-08-30 fix:Serial USB CDC RX
    - (Serial.c) fix receive payloads on USB CDC
    [Serial.c]
2025-09-02 feat: add PID parameters and update SERIAL_Handler for control gains
2025-09-04 fix:more than 64 bytes in USB CDC
    - USB 2.0으로 연결된 USB_CDC에서 패킷이 나누어져 입력되는 경우, 합쳐서 받도록 수정
    - USB 2.0에서 한 패킷은 64 byte이므로, 그 이상의 데이터는 나누어져 전송됨.
    - 기존 코드는 한 패킷만 처리 가능하여 최대 64 byte로 제한이 있었음.
    - 수정 코드는 나누어져 입력된 패킷을 조합하여 처리하도록 수정됨.
    - refactor : MiniLink header
    - LOG_MAVLINK_HEADER -> MINILINK_STX_CODE
    - serialRX.header.lenght 변경 : 기존에는 payload의 크기만 저장하였으나, 지금은 패킷의 크기를 저장하도록 수정. 프로토콜 규칙 준수하여 실수를 예방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
    [MiniLink.c, Serial.c]
2025-09-04 refactor:Param_type.h update
    - new Param_type.h using param xml converter
    - fix new header file
    [ICM42688P.c, config_PARM.c]
2025-09-04 copter moter mixed
    Author: Lee Hyeonje <leecurrent04@gmail.com>
    interactive rebase in progress; onto 2425602
    Last commands done (2 commands done):
    pick 837cbad # offset code testing
    pick ac48174 # copter moter mixed
    Next commands to do (2 remaining commands):
    pick 5ebf6ea # fix:Serial USB CDC RX
    pick 1639dbf # fix:serial revceive malloc bug
    You are currently rebasing branch 'icm42688p_offset_cali' on '2425602'.
    Changes to be committed:
    modified: Plane/Core/Inc/stm32f4xx_it.h
    modified: Plane/Core/Src/FC_Serial/MiniLink/config_PARM.c
    modified: Plane/Core/Src/FC_Servo/Servo.c
    modified: Plane/Core/Src/main.c
    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
    [Plane.ioc, Servo.c, config_PARM.c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]
2025-09-04 fix:Serial USB CDC RX
    - fix to revice payloads on USB CDC
    - minor fix
    Last commands done (3 commands done):
    Next command to do (1 remaining command):
    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
    [config_PARM.c]
2025-09-04 fix:serial revceive malloc bug
    - fix : double free() memory bug
    - refactor : SERIAL_receivedParse()
    - add : serialRX.flag.nack flag
    Last commands done (4 commands done):
    No commands remaining.
    modified: Plane/Core/Src/FC_Serial/Serial.c
    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
    [Serial.c, config_PARM.c]
2025-09-04 fix : attitude eular value
    - fix : msg.attitude
    - 쿼터니언 변환하는 과정에서 값이 많이 이상한듯
    - 오일러각으로 저장하도록 함
    [AHRS.c, Serial.c]

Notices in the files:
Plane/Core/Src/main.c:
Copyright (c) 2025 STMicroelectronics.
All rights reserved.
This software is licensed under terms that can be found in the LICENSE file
